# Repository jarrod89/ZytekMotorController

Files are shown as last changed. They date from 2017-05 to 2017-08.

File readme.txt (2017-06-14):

Motor control replacement board for Zytek 55KW motor.
Thanks go to James Hamond for his help in development.

Software is a modified version of Texas Instruments "Motorware" which is released under the BSD licence.

Hardware design is original work and is released under the BSD licence:

Copyright 2017 Jarrod Tuma

Redistribution and use in source and binary forms, with or without modification, are permitted provided that the following conditions are met:

1. Redistributions of source code must retain the above copyright notice, this list of conditions and the following disclaimer.

2. Redistributions in binary form must reproduce the above copyright notice, this list of conditions and the following disclaimer in the documentation and/or other materials provided with the distribution.

THIS SOFTWARE IS PROVIDED BY THE COPYRIGHT HOLDERS AND CONTRIBUTORS "AS IS" AND ANY EXPRESS OR IMPLIED WARRANTIES, INCLUDING, BUT NOT LIMITED TO, THE IMPLIED WARRANTIES OF MERCHANTABILITY AND FITNESS FOR A PARTICULAR PURPOSE ARE DISCLAIMED. IN NO EVENT SHALL THE COPYRIGHT HOLDER OR CONTRIBUTORS BE LIABLE FOR ANY DIRECT, INDIRECT, INCIDENTAL, SPECIAL, EXEMPLARY, OR CONSEQUENTIAL DAMAGES (INCLUDING, BUT NOT LIMITED TO, PROCUREMENT OF SUBSTITUTE GOODS OR SERVICES; LOSS OF USE, DATA, OR PROFITS; OR BUSINESS INTERRUPTION) HOWEVER CAUSED AND ON ANY THEORY OF LIABILITY, WHETHER IN CONTRACT, STRICT LIABILITY, OR TORT (INCLUDING NEGLIGENCE OR OTHERWISE) ARISING IN ANY WAY OUT OF THE USE OF THIS SOFTWARE, EVEN IF ADVISED OF THE POSSIBILITY OF SUCH DAMAGE.

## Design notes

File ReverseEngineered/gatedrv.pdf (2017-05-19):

High Side Feedback 1 2 | 3 4 | *

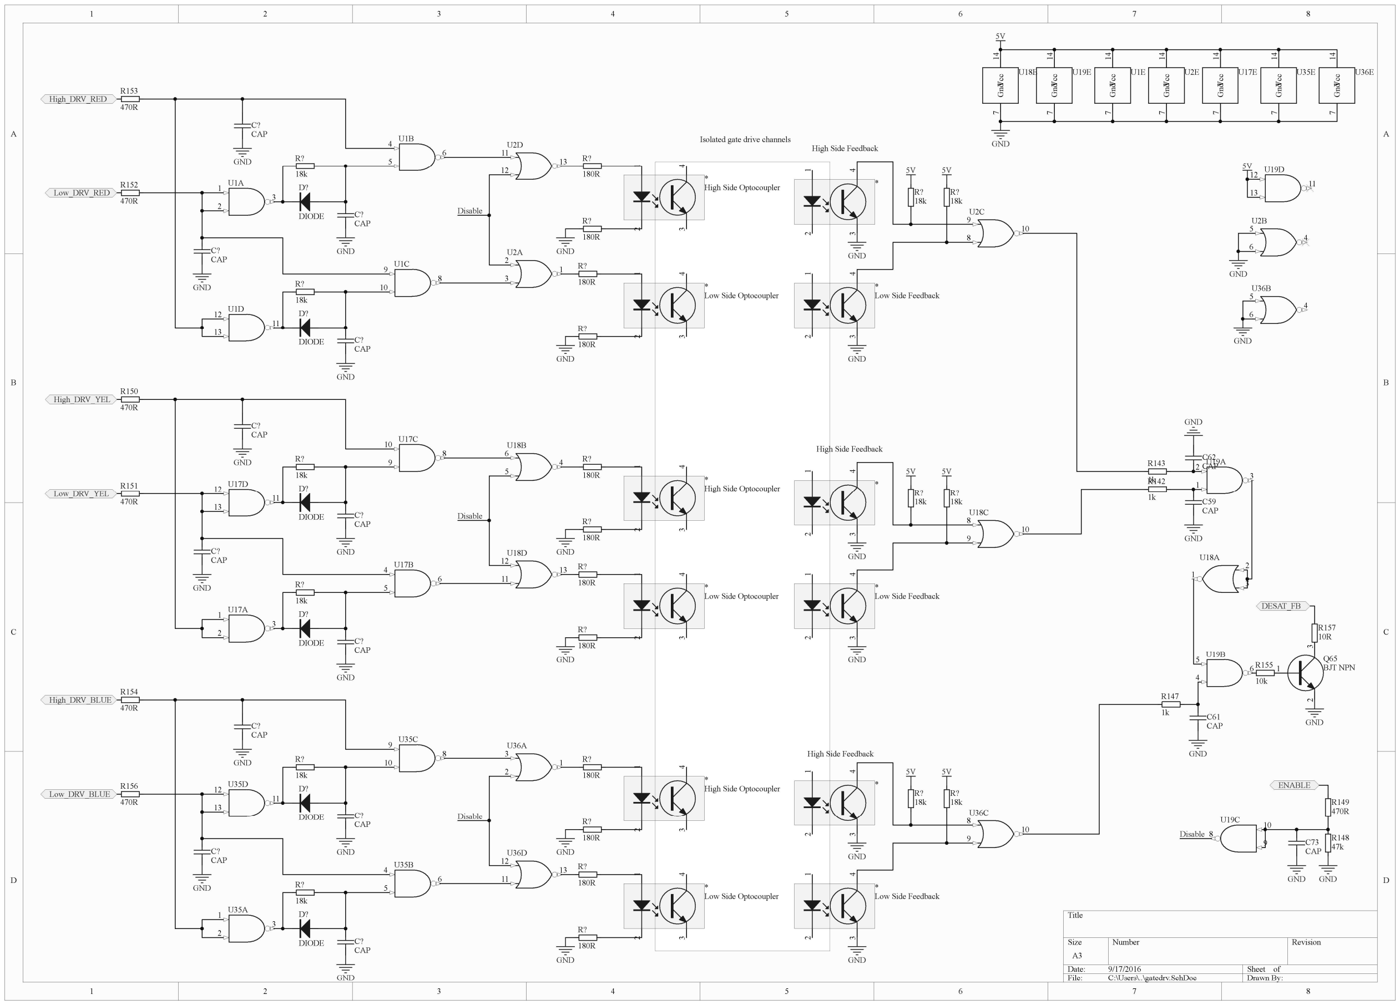
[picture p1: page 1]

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
Title
Size | Number | Revision
A3
Date: | 9/17/2016 | Sheet of
File: | C:\Users\..\gatedrv.SchDoc | Drawn By:

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
U1D | Gnd

### 7 Vcc 14

U1E

D?
DIODE

D?
DIODE

R?
18k

R153
470R

R?
18k

R152
470R

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
U2D | Gnd

### 7 Vcc 14

U2E
High_DRV_RED

Low_DRV_RED

R?
180R

R?
180R
R?
180R

R?
180R

1 23 4 *
High Side Optocoupler 1 2 | 3 4 | *

Low Side Optocoupler

GND

GND

GND ¹ ² | 3 4 | *

Low Side Feedback

R?
18k

R?
18k

5V 5V

GND

GND

R143
1k

C62
CAP
1

2
3

U19A

4

5
6

U19B

8
9

### 10 U19C

11

12
13

U19D Gnd

### 7 Vcc 14

U19E

GND

2
3

1

U18A

5

6
4

U18B

10

8
9

U18C

13
11

12

U18D | Gnd

### 7 Vcc 14

U18E

R147
1k C61 CAP

GND

R142
1k C59 CAP

GND

R155
10k

1 3 2
Q65
BJT NPN

GND

R157
10R

DESAT_FB

R148
47k C73
CAP
GND

R149
470R

GND

ENABLE

1
2

3

U17A

4
5

6

U17B

8
9

### 10 U17C

11

12
13
U17D | Gnd

### 7 Vcc 14

U17E

1
2

3

U35A

4
5

6

U35B

8

9
10

U35C

11

12
13
U35D | Gnd

### 7 Vcc 14

U35E

2

3
1

U36A

5
6

4

U36B

10

8
9

U36C

13
11

12

U36D | Gnd

### 7 Vcc 14

U36E

D?
DIODE

D?
DIODE

R?
18k

R150
470R

R?
18k

R151
470R

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
High_DRV_YEL

Low_DRV_YEL

R?
180R

R?
180R
R?
180R

R?
180R

1 23 4 *
High Side Optocoupler 1 2 | 3 4 | *

Low Side Optocoupler

GND

GND | 1 2 | 3 4 | *
High Side Feedback 1 2 | 3 4 | *

Low Side Feedback

R?
18k

R?
18k

5V 5V

GND

GND

D?
DIODE

D?
DIODE

R?
18k

R154
470R

R?
18k

R156
470R

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
High_DRV_BLUE

Low_DRV_BLUE

R?
180R

R?
180R
R?
180R

R?
180R

1 23 4 *
High Side Optocoupler 1 2 | 3 4 | *

Low Side Optocoupler

GND

GND | 1 2 | 3 4 | *
| High Side Feedback 1 2 | 3 4 | *

Low Side Feedback

R?
18k

R?
18k

5V 5V

GND

GND

5V

GND

5V

GND

Disable

Disable

Disable
Disable

Isolated gate drive channels

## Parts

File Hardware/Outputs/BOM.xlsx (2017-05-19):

Quantity | Designator | Comment | Footprint | Parameter | Manufacturer 1 | Manufacturer 2 | Manufacturer 3 | Manufacturer 4
1 | U13 | D-FLIPFLOP | SOT23-6 |  | TI SN74LVC1G175
1 | U11.2 | BTS-6143 | TO252-5-11
1 | U10 | SI88244ED-IS | SLAB-SOIC-20-WB_N |  | Silicon Labs
1 | U9 | SN74LVC1G04DBV | SOT23-5
1 | U7 | 4:1 MUX | SOIC16
2 | U5, U6 | 74AHC08 | SOIC14
4 | U4.3, U4.4, U4.5, U4.6 | OP-AMP | SOT23-5 | >1MHz, 3.3V, rail-rail. | Microchip MCP6283T | Fairchild FAN4174IS5X
6 | U3.3, U3.4, U3.5, U3.6, U8, U12 | MCP6562 | MSOP8 |  | Microchip MCP6562, Microchip MCP6562, Microchip MCP6562, Microchip MCP6562, Microchip Technology, Microchip Technology
1 | U2.2 | AP2114H-3.3TRG1DICT-ND | SOT223
1 | U1.2 | AOZ1282 | SOT23-6 | 1.2A, 4.5V-36V input, 450KHz | Alpha & Omega AOZ1282CI
1 | T1 | 2.5uH 4:11 | RM5/I
16 | R86, R87, R88, R89, R90, R91, R92, R93, R94, R96, R97, R99, R102, R103, R104, R105 | 1M | 1206 | High Voltage | Rohm Semiconductor
4 | R82, R83, R84, R85 | 130R | 0603
1 | R80 | 13.3k | 0603
2 | R79, R81 | 49.9k | 0603
1 | R78 | 100R | 0603
2 | R45.2, R47 | 47k | 0805 | <1%, Thick film, 63mW
5 | R40, R95, R98, R100, R101 | 2k | 0603 | 1%, Thick or Metal Film, 63mW, [NoValue], [NoValue], [NoValue], [NoValue]
4 | R33, R35, R37, R39 | 100k | 0603 | 1%, Thick or Metal Film, 63mW
13 | R19, R20, R21, R22, R23, R28, R29, R30, R31, R32, R34, R36, R38 | 56 | 0603 | 1%, Thick or Metal Film, 63mW, 1%, Thick or Metal Film, 63mW, 1%, Thick or Metal Film, 63mW, 1%, Thick or Metal Film, 63mW, [NoValue], 1%, Thick or Metal Film, 63mW, 1%, Thick or Metal Film, 63mW, 1%, Thick or Metal Film, 63mW, 1%, Thick or Metal Film, 63mW, 1%, Thick or Metal Film, 63mW, 1%, Thick or Metal Film, 63mW, 1%, Thick or Metal Film, 63mW, 1%, Thick or Metal Film, 63mW
4 | R11.3, R11.4, R11.5, R11.6 | 20 | 1206 | 1%, Thick or Metal Film, 63mW
5 | R10.3, R10.4, R10.5, R10.6, R49 | 100 | 0603 | 1%, Thick or Metal Film, 63mW
12 | R8.3, R8.4, R8.5, R8.6, R12.3, R12.4, R12.5, R12.6, R53.3, R53.4, R53.5, R53.6 | 3k3 | 0603 | 1%, Thick or Metal Film, 63mW
17 | R5.3, R5.4, R5.5, R5.6, R6.3, R6.4, R6.5, R6.6, R15, R16, R17, R18, R24, R25, R26, R27, R44.2 | 10k | 0603 | 1%, Thick or Metal Film, 63mW, 1%, Thick or Metal Film, 63mW, 1%, Thick or Metal Film, 63mW, 1%, Thick or Metal Film, 63mW, 1%, Thick or Metal Film, 63mW, 1%, Thick or Metal Film, 63mW, 1%, Thick or Metal Film, 63mW, 1%, Thick or Metal Film, 63mW, [NoValue], [NoValue], [NoValue], [NoValue], [NoValue], [NoValue], [NoValue], [NoValue], 1%, Thick or Metal Film, 63mW
8 | R4.3, R4.4, R4.5, R4.6, R7.3, R7.4, R7.5, R7.6 | 220R | 0603 | 1%, Thick or Metal Film, 63mW
1 | R3.2 | 68k | 0603 | <1%, Thick film, 63mW
1 | R2.2 | 13k | 0603 | <1%, Thick film, 63mW
24 | R1.2, R9.3, R9.4, R9.5, R9.6, R13.3, R13.4, R13.5, R13.6, R14, R41, R42, R43, R46, R48, R50, R51, R52, R54, R56, R106, R107, R108, R109 | 1k | 0603 | <1%, Thick film, 63mW, 1%, Thick or Metal Film, 63mW, 1%, Thick or Metal Film, 63mW, 1%, Thick or Metal Film, 63mW, 1%, Thick or Metal Film, 63mW, 1%, Thick or Metal Film, 63mW, 1%, Thick or Metal Film, 63mW, 1%, Thick or Metal Film, 63mW, 1%, Thick or Metal Film, 63mW, 1%, Thick or Metal Film, 63mW, [NoValue], [NoValue], [NoValue], [NoValue], [NoValue], [NoValue], [NoValue], [NoValue], [NoValue], [NoValue], [NoValue], [NoValue], [NoValue], [NoValue]
1 | Q1.2 | nmos | SOT23
8 | P1, P2, P3, P4, P5, P6, P7, P8 | HEADER 10 | HDR10
4 | L8, L9, L10, L11 | 1m | 0805 | Inductor, 4u7, 20%, >100mA | Taiyo Yuden LBR2012T4R7M | Abracon AIML-0805-4R7K-T | Bourns CV201210-4R7K | TDK MLZ2012N4R7L
1 | L6 | 4u7 | 0805 | Inductor, 4u7, 20%, >100mA | Taiyo Yuden LBR2012T4R7M | Abracon AIML-0805-4R7K-T | Bourns CV201210-4R7K | TDK MLZ2012N4R7L
2 | L1.2, L2.2 | 22u, 1A | 2220 | INDUCTOR 22uH >1A 1210
1 | J13 | HEADER 5 | HDR5-5mm
1 | J6 | Header 17X2 | HDR2X17_2mm
1 | J5 | Header 16 | HDR1X16
1 | J1 | Header 25X2 | HDR2X20_2mm
1 | F1.2 | ?A | 1206
3 | D13, D14, D15 | LED | 0603_LED
9 | D5, D6, D7, D8, D9, D10, D11, D12, D16 | DIODE | D-0603
1 | D4 | DIODE SCHOTTKY | SOD323-AK
2 | D3, D17 |  | SOD323-AK | Signal, >=200mA, SOD323, Vr>=75V
1 | D2.2 | Schottky | DO214AC | DIODE SHOTTKY >30V >0.2A | Micro Commercial Co SD103AWS-TP
1 | D1.2 | ZENER | DO214AC
4 | C74, C75, C76, C77 | 220n | 0603
1 | C72 | 1n5 | 0603 | 10n, 0603, 50V, <20%, X7R Ceramic | Murata GRM188R71H103KA01D | AVX 06035C103KAT2A | TDK C1608X7R1H103J
1 | C69 | 100p | 0603 | 10n, 0603, 50V, <20%, X7R Ceramic | Murata GRM188R71H103KA01D | AVX 06035C103KAT2A | TDK C1608X7R1H103J
4 | C22.3, C22.4, C22.5, C22.6 | 3n3 | 0603
12 | C21.3, C21.4, C21.5, C21.6, C73, C78, C79, C80, C81, C82, C83, C84 | 470p | 0603
12 | C9.2, C16.2, C26, C27, C28, C29, C30, C31, C32, C33, C68, C71 | 10n | 0603 | 100n, 0603, 50V, <20%, X7R Ceramic, 10n, 0603, 50V, <20%, X7R Ceramic, [NoValue], [NoValue], [NoValue], [NoValue], [NoValue], [NoValue], [NoValue], [NoValue], [NoValue], [NoValue] | Murata GRM188R71H104KA93D, Murata GRM188R71H103KA01D, [NoValue], [NoValue], [NoValue], [NoValue], [NoValue], [NoValue], [NoValue], [NoValue], [NoValue], [NoValue] | TDK C1608X7R1H104K, AVX 06035C103KAT2A, [NoValue], [NoValue], [NoValue], [NoValue], [NoValue], [NoValue], [NoValue], [NoValue], [NoValue], [NoValue] | AVX 06035C104KAT2A, TDK C1608X7R1H103J, [NoValue], [NoValue], [NoValue], [NoValue], [NoValue], [NoValue], [NoValue], [NoValue], [NoValue], [NoValue] | Kemet C0603C104J5RACTU-ND
44 | C4.2, C5.2, C8.2, C12.2, C14.2, C17.3, C17.4, C17.5, C17.6, C18.3, C18.4, C18.5, C18.6, C19.3, C19.4, C19.5, C19.6, C20.3, C20.4, C20.5, C20.6, C23.3, C23.4, C23.5, C23.6, C24.3, C24.4, C24.5, C24.6, C34, C35, C36, C37, C38, C39, C40, C41, C42, C43, C66, C67, C70, C85, C86 | 100n | 0603 | 100n, 0603, 50V, <20%, X7R Ceramic, 100n, 0603, 50V, <20%, X7R Ceramic, 100n, 0603, 50V, <20%, X7R Ceramic, [NoValue], 470n, 0603, >=16V, <20%, X7R Ceramic, [NoValue], [NoValue], [NoValue], [NoValue], [NoValue], [NoValue], [NoValue], [NoValue], [NoValue], [NoValue], [NoValue], [NoValue], [NoValue], [NoValue], [NoValue], [NoValue], [NoValue], [NoValue], [NoValue], [NoValue], [NoValue], [NoValue], [NoValue], [NoValue], [NoValue], [NoValue], [NoValue], [NoValue], [NoValue], [NoValue], [NoValue], [NoValue], [NoValue], [NoValue], [NoValue], [NoValue], [NoValue], [NoValue], [NoValue] | Murata GRM188R71H104KA93D, Murata GRM188R71H104KA93D, Murata GRM188R71H104KA93D, [NoValue], Murata GCM188R71C474KA55D, [NoValue], [NoValue], [NoValue], [NoValue], [NoValue], [NoValue], [NoValue], [NoValue], [NoValue], [NoValue], [NoValue], [NoValue], [NoValue], [NoValue], [NoValue], [NoValue], [NoValue], [NoValue], [NoValue], [NoValue], [NoValue], [NoValue], [NoValue], [NoValue], [NoValue], [NoValue], [NoValue], [NoValue], [NoValue], [NoValue], [NoValue], [NoValue], [NoValue], [NoValue], [NoValue], [NoValue], [NoValue], [NoParam], [NoParam] | TDK C1608X7R1H104K, TDK C1608X7R1H104K, TDK C1608X7R1H104K, [NoValue], Taiyo EMK107B7474KA-T, [NoValue], [NoValue], [NoValue], [NoValue], [NoValue], [NoValue], [NoValue], [NoValue], [NoValue], [NoValue], [NoValue], [NoValue], [NoValue], [NoValue], [NoValue], [NoValue], [NoValue], [NoValue], [NoValue], [NoValue], [NoValue], [NoValue], [NoValue], [NoValue], [NoValue], [NoValue], [NoValue], [NoValue], [NoValue], [NoValue], [NoValue], [NoValue], [NoValue], [NoValue], [NoValue], [NoValue], [NoValue], [NoParam], [NoParam] | AVX 06035C104KAT2A, AVX 06035C104KAT2A, AVX 06035C104KAT2A, [NoValue], Kemet C0603C474K4RACTU, C0603C474K4RAC, [NoValue], [NoValue], [NoValue], [NoValue], [NoValue], [NoValue], [NoValue], [NoValue], [NoValue], [NoValue], [NoValue], [NoValue], [NoValue], [NoValue], [NoValue], [NoValue], [NoValue], [NoValue], [NoValue], [NoValue], [NoValue], [NoValue], [NoValue], [NoValue], [NoValue], [NoValue], [NoValue], [NoValue], [NoValue], [NoValue], [NoValue], [NoValue], [NoValue], [NoValue], [NoValue], [NoValue], [NoValue], [NoParam], [NoParam] | Kemet C0603C104J5RACTU-ND, Kemet C0603C104J5RACTU-ND, Kemet C0603C104J5RACTU-ND, [NoParam], TDK C1608X7R1C474M, [NoParam], [NoParam], [NoParam], [NoParam], [NoParam], [NoParam], [NoParam], [NoParam], [NoParam], [NoParam], [NoParam], [NoParam], [NoParam], [NoParam], [NoParam], [NoParam], [NoParam], [NoParam], [NoParam], [NoParam], [NoParam], [NoParam], [NoParam], [NoParam], [NoParam], [NoParam], [NoParam], [NoParam], [NoParam], [NoParam], [NoParam], [NoParam], [NoParam], [NoParam], [NoParam], [NoParam], [NoParam], [NoParam], [NoParam]
13 | C1.2, C2.2, C3.2, C6.2, C7.2, C10.2, C11.2, C13.2, C15.2, C25, C63, C64, C65 | 10u | 0805 | [NoValue], [NoValue], [NoValue], 10uF, 0805, =>6.3V, <=10%, X5R Ceramic, 10uF, 0805, =>6.3V, <=10%, X5R Ceramic, 10uF, 0805, =>6.3V, <=10%, X5R Ceramic, 10uF, 0805, =>6.3V, <=10%, X5R Ceramic, 10uF, 0805, =>6.3V, <=10%, X5R Ceramic, [NoValue], [NoValue], [NoValue], [NoValue], [NoValue]

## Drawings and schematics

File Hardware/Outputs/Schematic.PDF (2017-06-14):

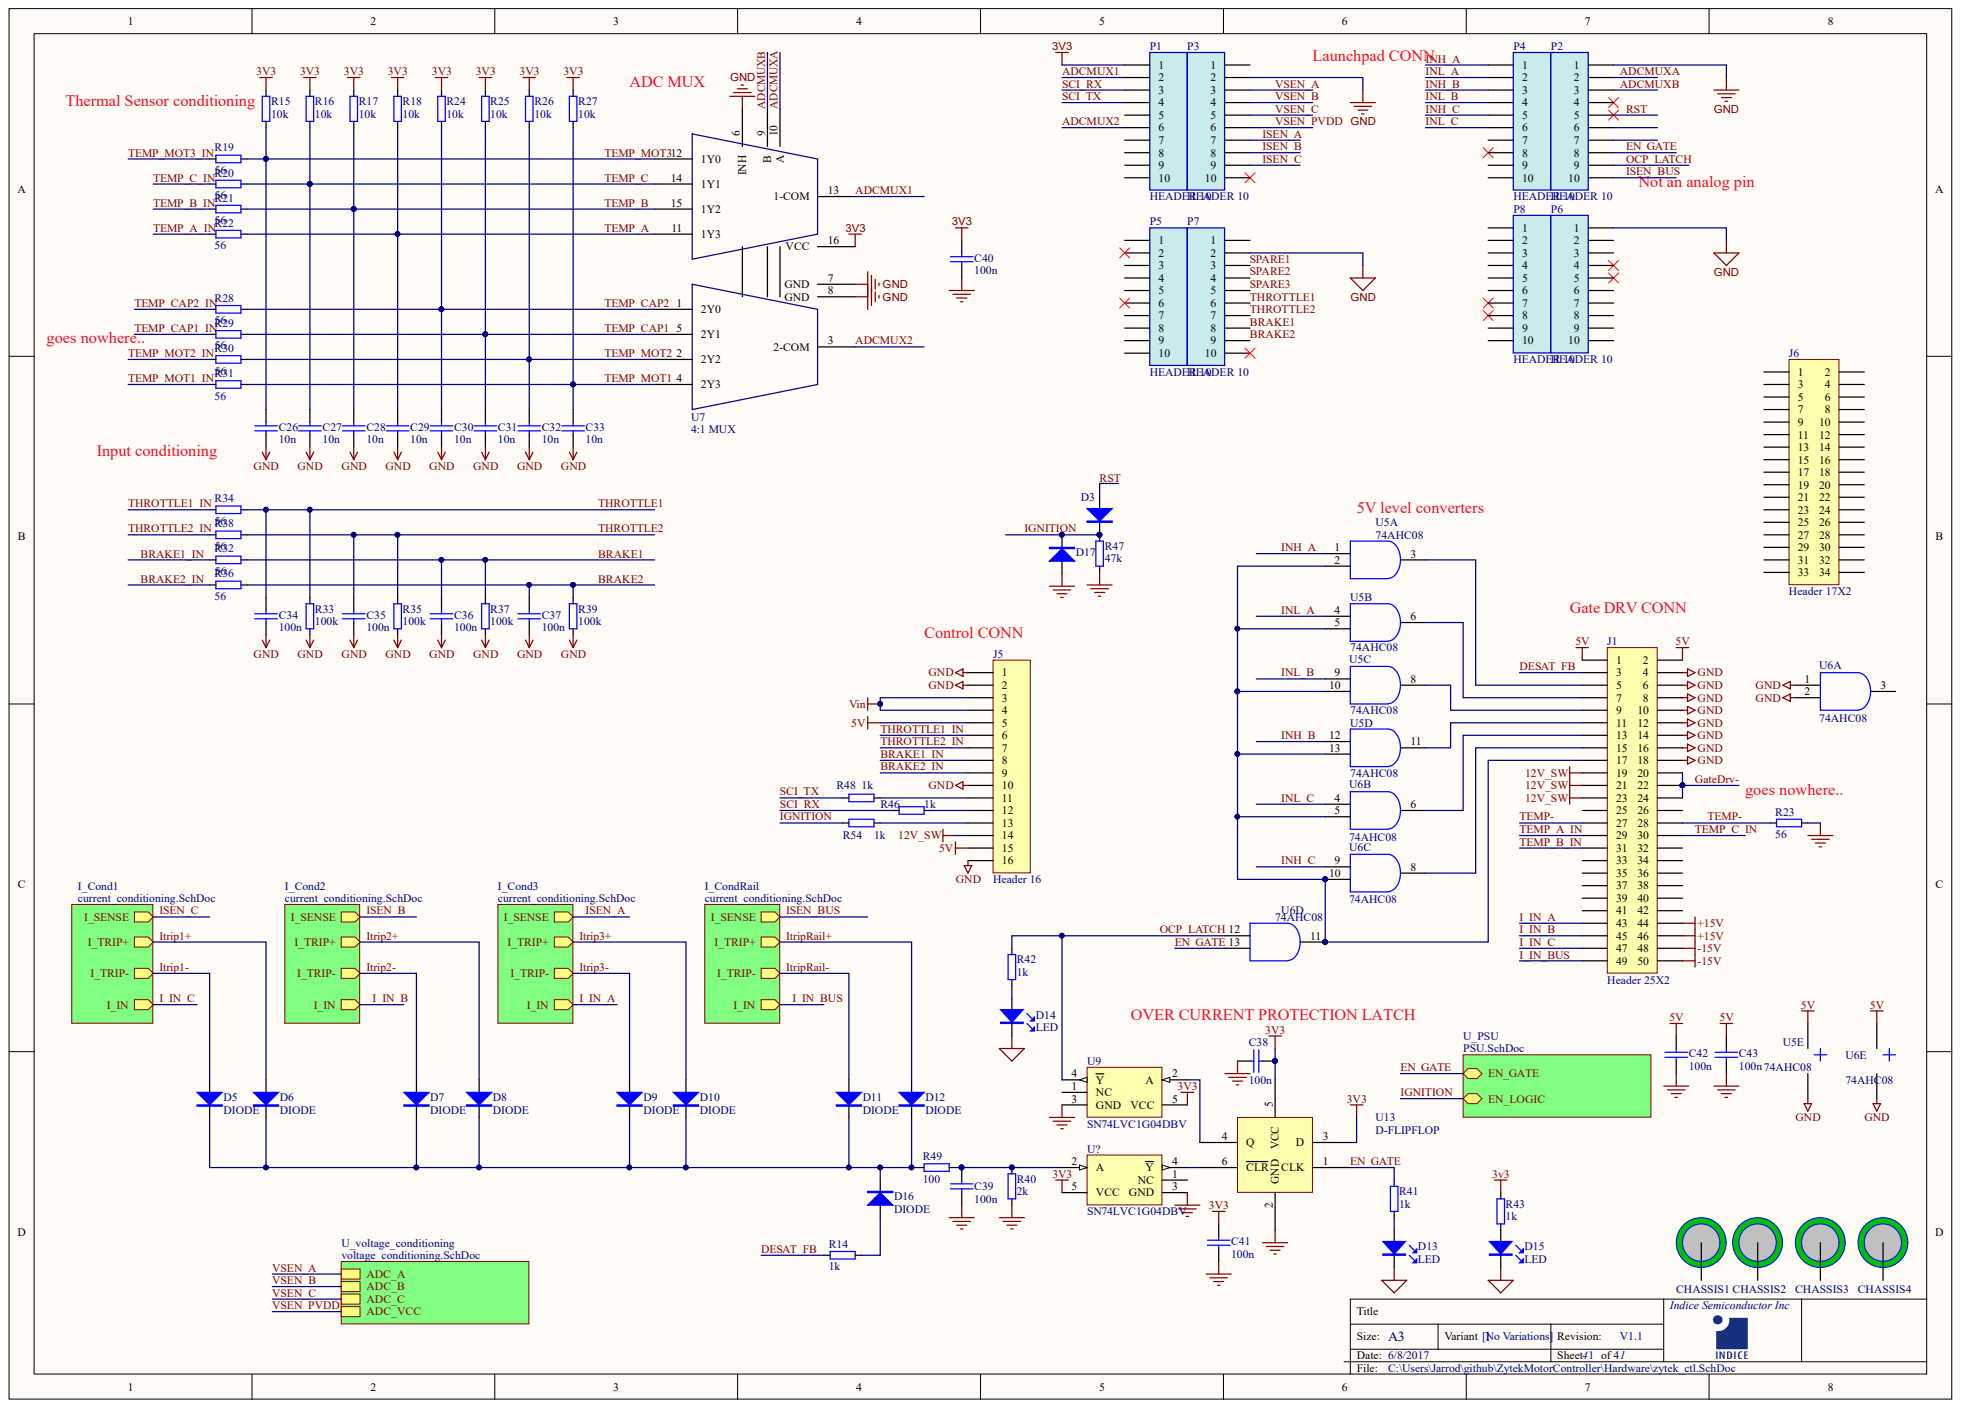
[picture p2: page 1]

OVER CURRENT PROTECTION LATCH

Title | Indice Semiconductor Inc

Size: A3 | Variant [No Variations] | Revision: V1.1
Date: 6/8/2017 | | Sheet 41 of 41

C:\Users\Jarrod\github\ZytekMotorController\Hardware\zytek_ctl.SchDoc

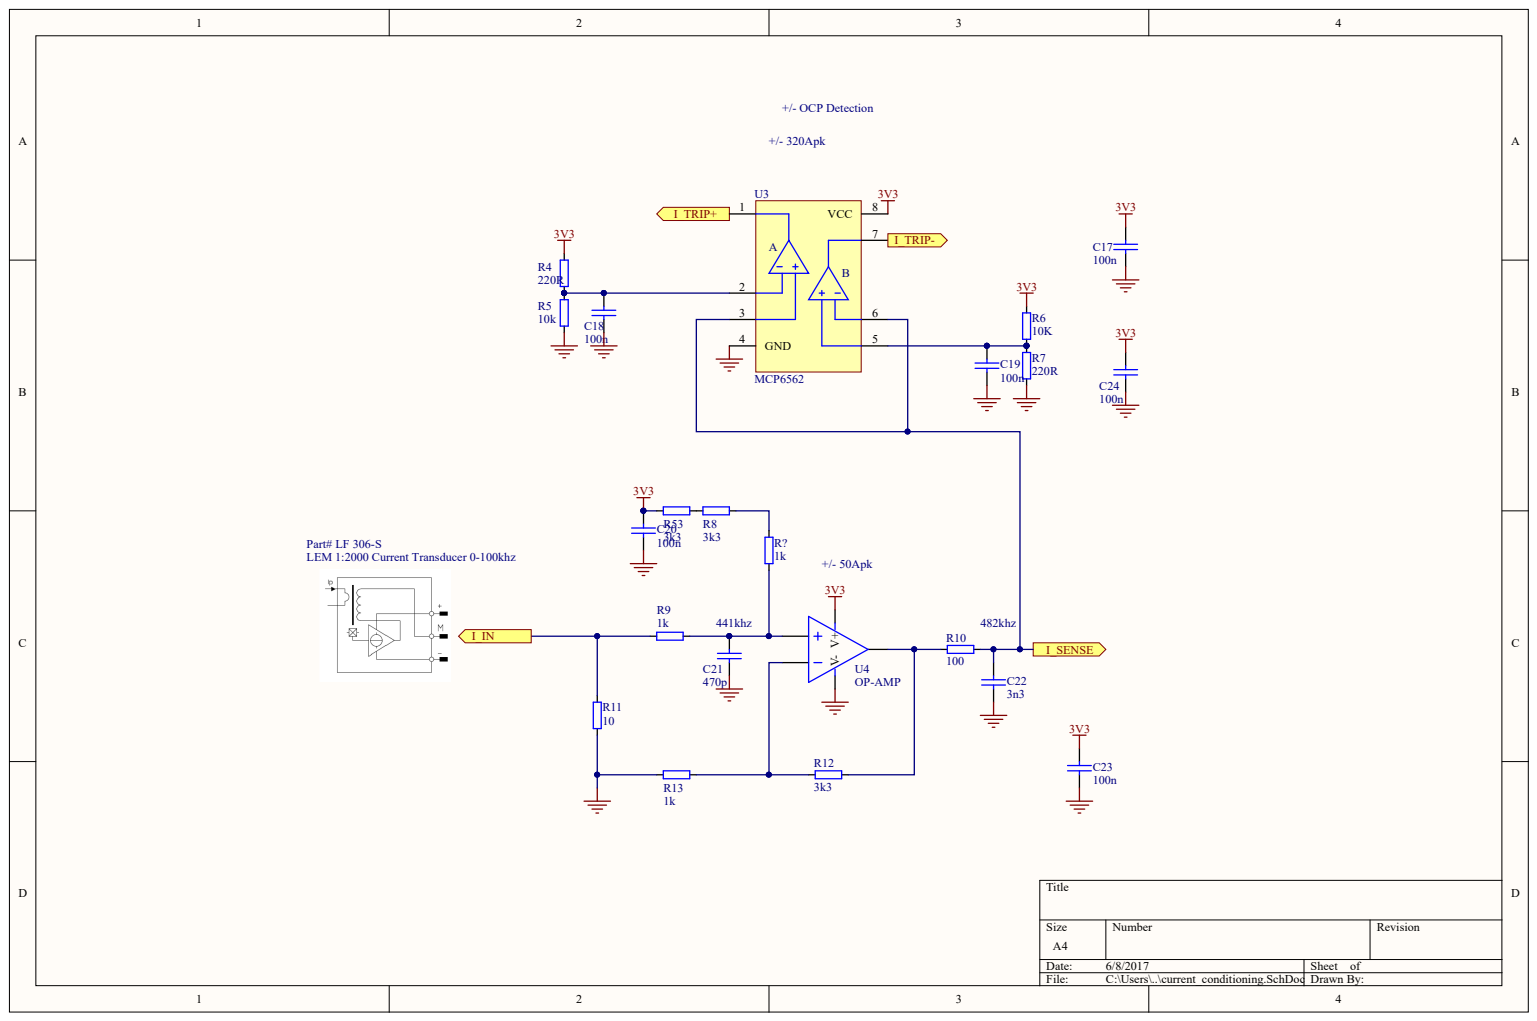
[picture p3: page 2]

U4 OP-AMP

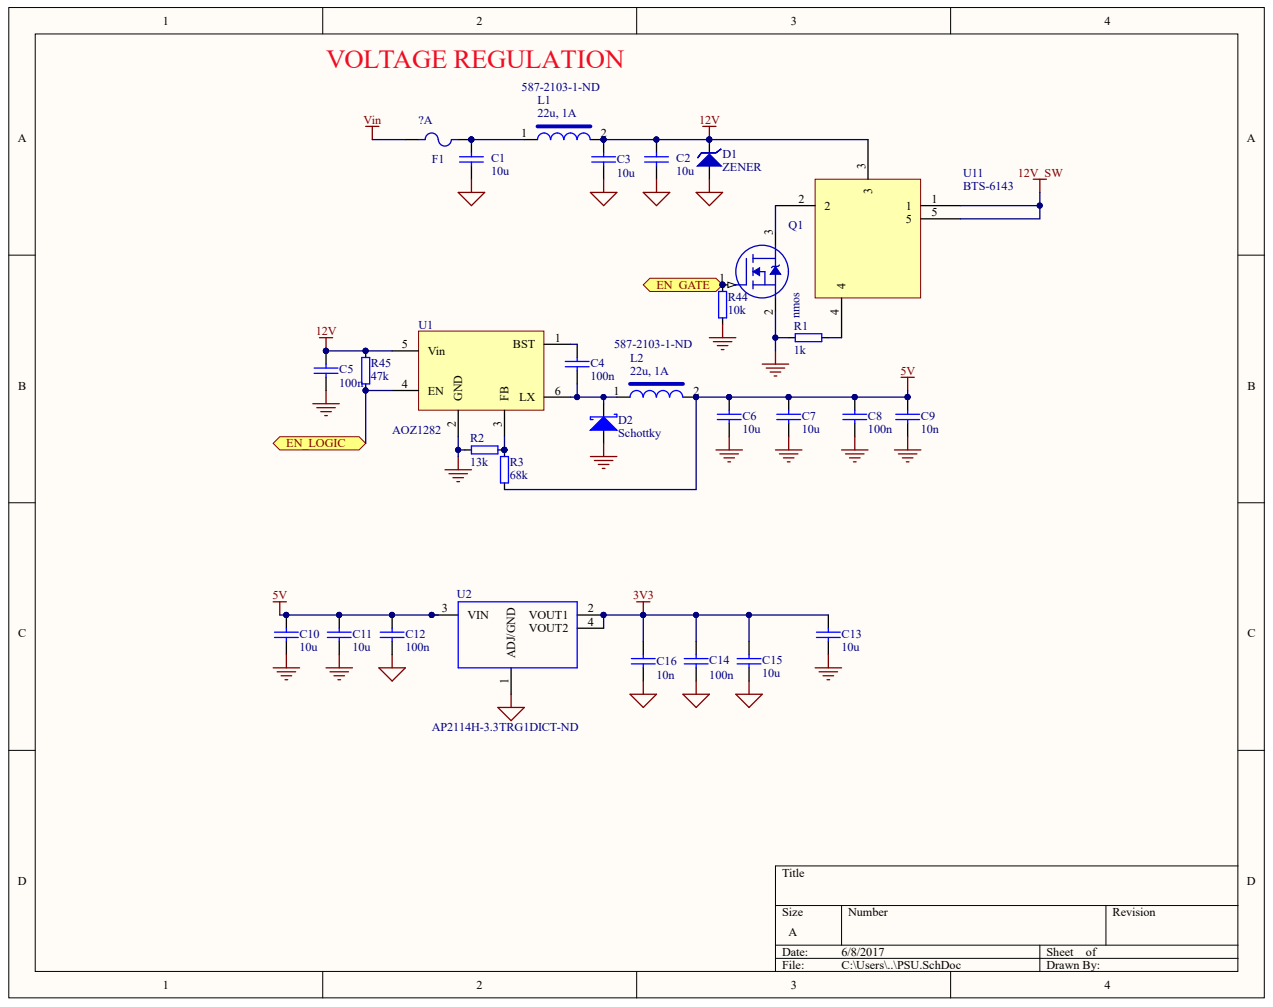
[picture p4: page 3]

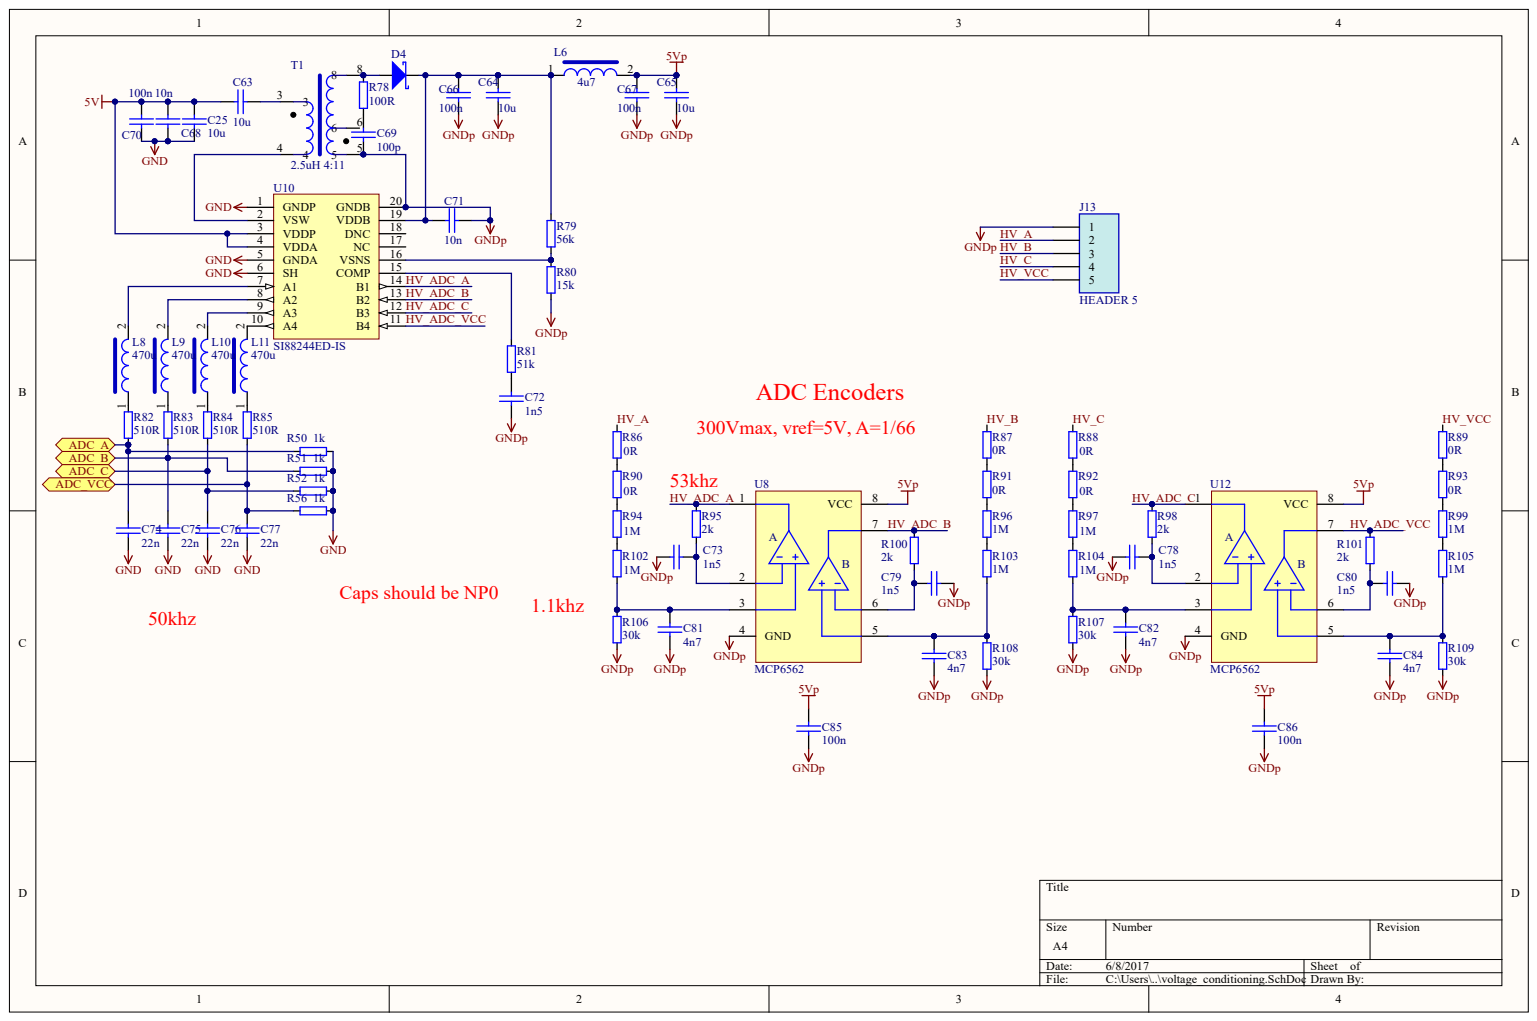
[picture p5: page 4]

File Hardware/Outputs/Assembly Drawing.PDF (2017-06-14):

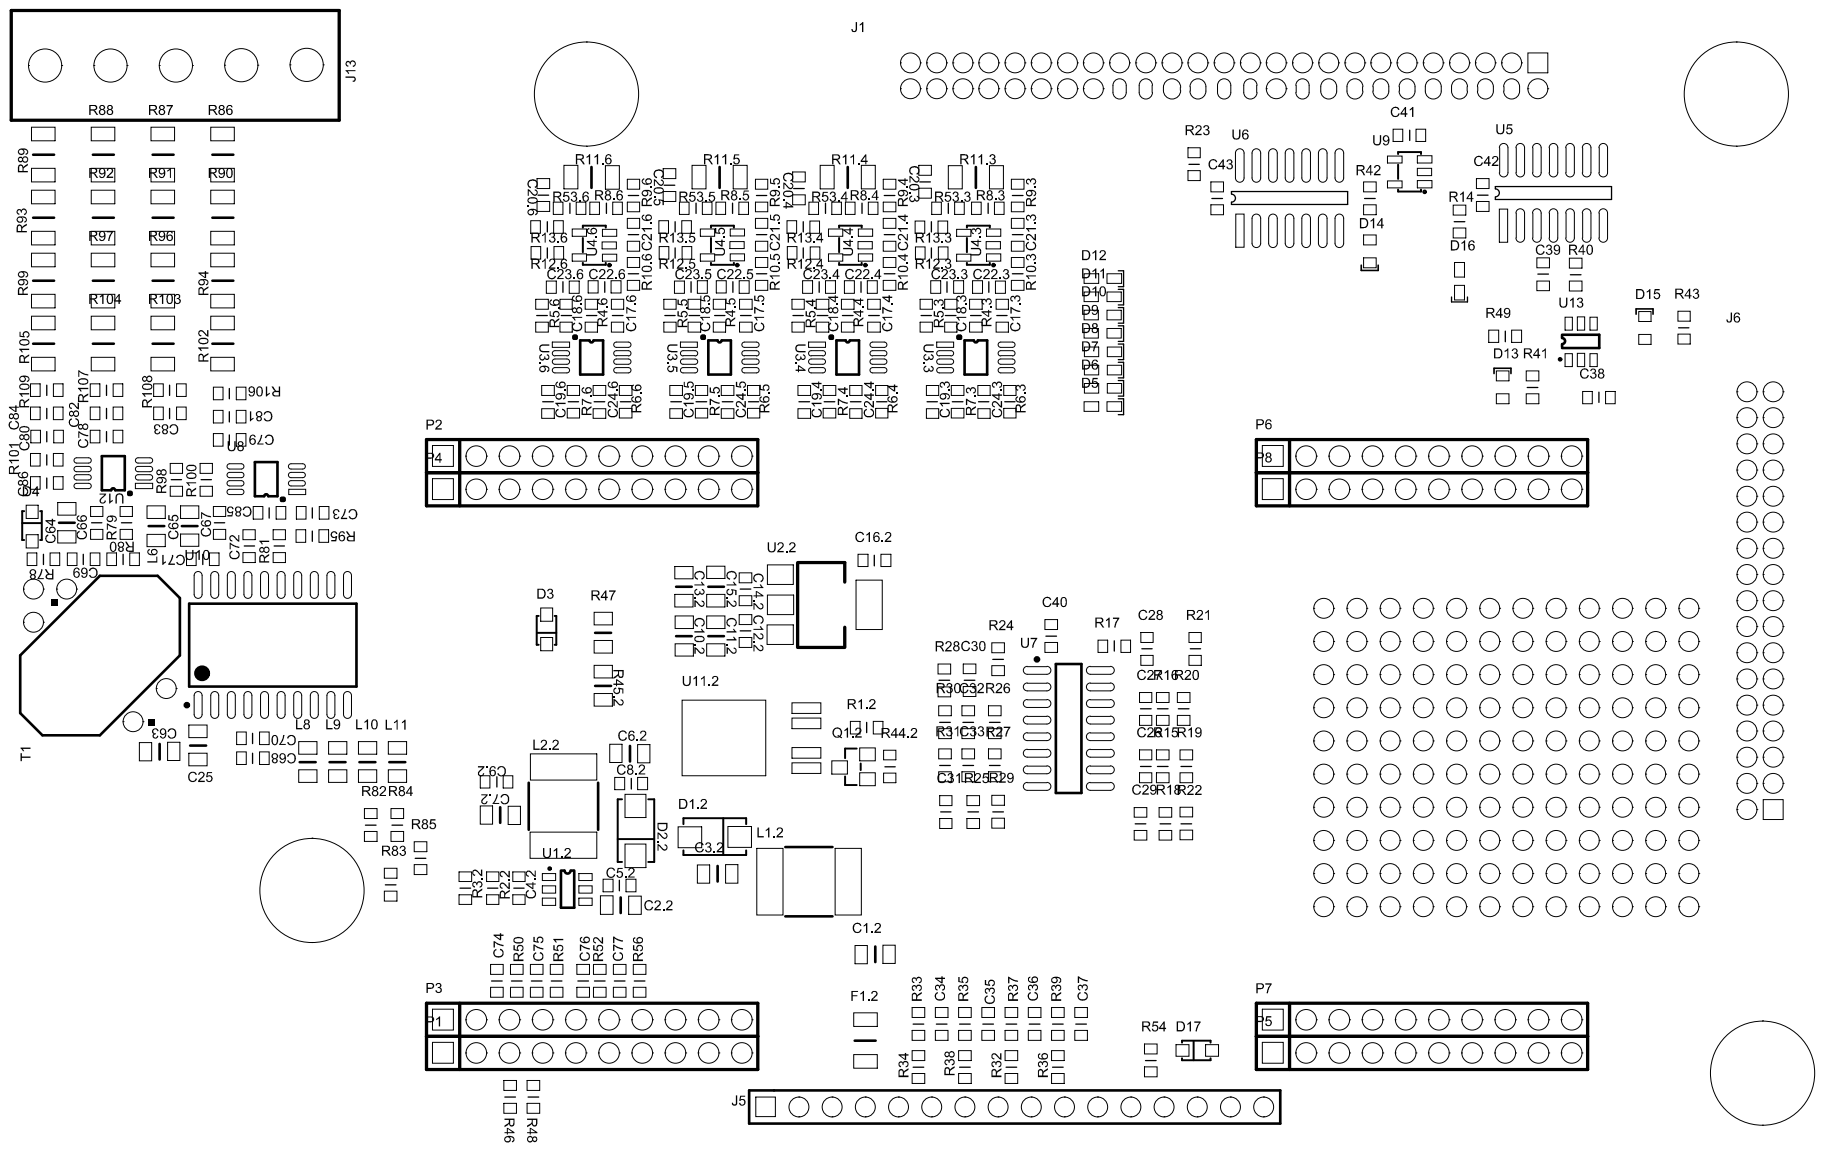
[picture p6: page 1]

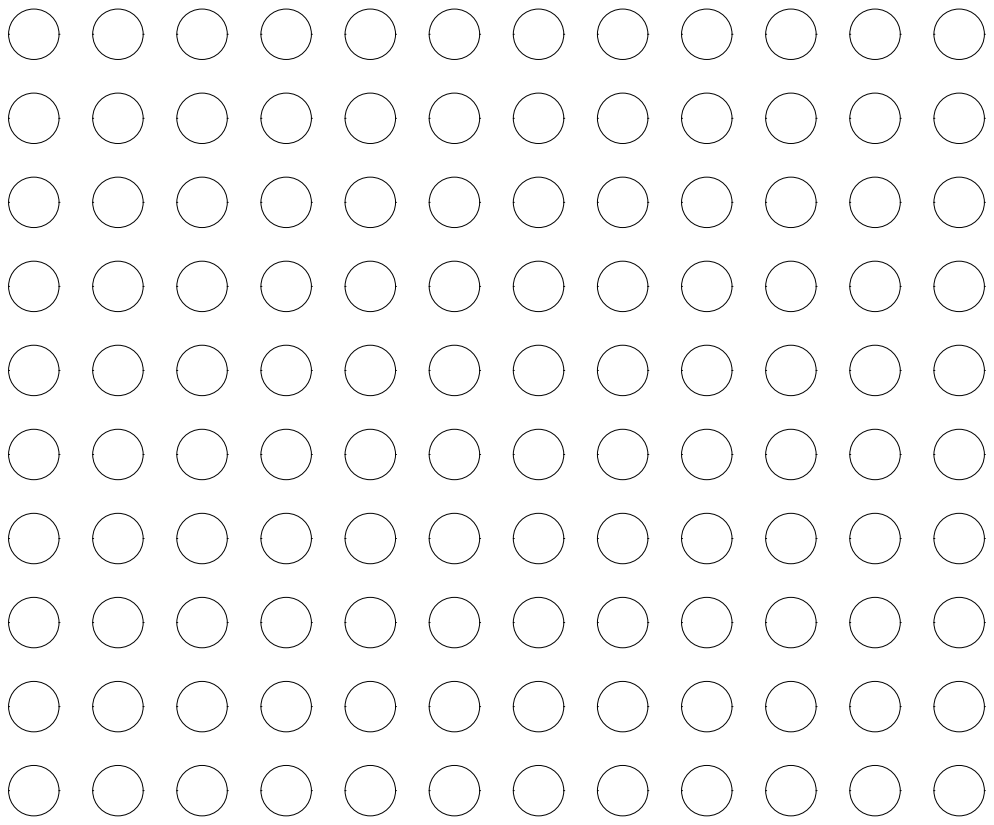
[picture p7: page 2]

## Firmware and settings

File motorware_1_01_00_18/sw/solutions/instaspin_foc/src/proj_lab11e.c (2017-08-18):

/* --COPYRIGHT--,BSD
 * Copyright (c) 2015, Texas Instruments Incorporated
 * All rights reserved.
 *
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
 * *  Redistributions of source code must retain the above copyright
 *    notice, this list of conditions and the following disclaimer.
 *
 * *  Redistributions in binary form must reproduce the above copyright
 *    notice, this list of conditions and the following disclaimer in the
 *    documentation and/or other materials provided with the distribution.
 *
 * *  Neither the name of Texas Instruments Incorporated nor the names of
 *    its contributors may be used to endorse or promote products derived
 *    from this software without specific prior written permission.
 *
 * THIS SOFTWARE IS PROVIDED BY THE COPYRIGHT HOLDERS AND CONTRIBUTORS "AS IS"
 * AND ANY EXPRESS OR IMPLIED WARRANTIES, INCLUDING, BUT NOT LIMITED TO,
 * THE IMPLIED WARRANTIES OF MERCHANTABILITY AND FITNESS FOR A PARTICULAR
 * PURPOSE ARE DISCLAIMED. IN NO EVENT SHALL THE COPYRIGHT OWNER OR
 * CONTRIBUTORS BE LIABLE FOR ANY DIRECT, INDIRECT, INCIDENTAL, SPECIAL,
 * EXEMPLARY, OR CONSEQUENTIAL DAMAGES (INCLUDING, BUT NOT LIMITED TO,
 * PROCUREMENT OF SUBSTITUTE GOODS OR SERVICES; LOSS OF USE, DATA, OR PROFITS;
 * OR BUSINESS INTERRUPTION) HOWEVER CAUSED AND ON ANY THEORY OF LIABILITY,
 * WHETHER IN CONTRACT, STRICT LIABILITY, OR TORT (INCLUDING NEGLIGENCE OR
 * OTHERWISE) ARISING IN ANY WAY OUT OF THE USE OF THIS SOFTWARE,
 * EVEN IF ADVISED OF THE POSSIBILITY OF SUCH DAMAGE.
 * --/COPYRIGHT--*/
//! \file   solutions/instaspin_foc/src/proj_lab011e.c
//! \brief Hall sensor start-up with transition to FAST for InstaSPIN-FOC
//!
//! (C) Copyright 2015, Texas Instruments, Inc.

//! \defgroup PROJ_LAB11e PROJ_LAB11e
//@{

//! \defgroup PROJ_LAB11e_OVERVIEW Project Overview
//!
//! Hall sensor start-up with transition to FAST for InstaSPIN-FOC
//! 
//!

// **************************************************************************
// the includes

// system includes
#include <math.h>
#include "main.h"


#ifdef FLASH
#pragma CODE_SECTION(mainISR,"ramfuncs");
#pragma CODE_SECTION(runSetTrigger,"ramfuncs");
#pragma CODE_SECTION(runFieldWeakening,"ramfuncs");
#pragma CODE_SECTION(runCurrentReconstruction,"ramfuncs");
#pragma CODE_SECTION(angleDelayComp,"ramfuncs");
#pragma CODE_SECTION(HALLBLDC_State_Check,"ramfuncs");
#pragma CODE_SECTION(HALLBLDC_Ctrl_PwmSet,"ramfuncs");
#pragma CODE_SECTION(HALLBLDC_Ctrl_Run,"ramfuncs");
#endif

// Include header files used in the main function

// **************************************************************************
// the defines

// **************************************************************************
// the globals

CLARKE_Handle   clarkeHandle_I;               //!< the handle for the current Clarke transform
CLARKE_Obj      clarke_I;                     //!< the current Clarke transform object

CLARKE_Handle   clarkeHandle_V;               //!< the handle for the voltage Clarke transform
CLARKE_Obj      clarke_V;                     //!< the voltage Clarke transform object

EST_Handle      estHandle;                    //!< the handle for the estimator

FW_Handle       fwHandle;
FW_Obj          fw;

PID_Obj         pid[4];                       //!< three handles for PID controllers 0 - Speed, 1 - Id, 2 - Iq
PID_Handle      pidHandle[4];                 //!< three objects for PID controllers 0 - Speed, 1 - Id, 2 - Iq
uint16_t        pidCntSpeed;                  //!< count variable to decimate the execution of the speed PID controller

IPARK_Handle    iparkHandle;                  //!< the handle for the inverse Park transform
IPARK_Obj       ipark;                        //!< the inverse Park transform object

FILTER_FO_Handle  filterHandle[6];            //!< the handles for the 3-current and 3-voltage filters for offset calculation
FILTER_FO_Obj     filter[6];                  //!< the 3-current and 3-voltage filters for offset calculation

SVGENCURRENT_Obj     svgencurrent;
SVGENCURRENT_Handle  svgencurrentHandle;

SVGEN_Handle    svgenHandle;                  //!< the handle for the space vector generator
SVGEN_Obj       svgen;                        //!< the space vector generator object

TRAJ_Handle     trajHandle_Id;                //!< the handle for the id reference trajectory
TRAJ_Obj        traj_Id;                      //!< the id reference trajectory object

TRAJ_Handle     trajHandle_spd;               //!< the handle for the speed reference trajectory
TRAJ_Obj        traj_spd;                     //!< the speed reference trajectory object

#ifdef CSM_ENABLE
#pragma DATA_SECTION(halHandle,"rom_accessed_data");
#endif

HAL_Handle      halHandle;                    //!< the handle for the hardware abstraction layer (HAL)

HAL_PwmData_t   gPwmData = {_IQ(0.0), _IQ(0.0), _IQ(0.0)};       //!< contains the three pwm values -1.0 - 0%, 1.0 - 100%

HAL_AdcData_t   gAdcData;                     //!< contains three current values, three voltage values and one DC buss value

MATH_vec3       gOffsets_I_pu = {_IQ(0.0), _IQ(0.0), _IQ(0.0)};  //!< contains the offsets for the current feedback

MATH_vec3       gOffsets_V_pu = {_IQ(0.0), _IQ(0.0), _IQ(0.0)};  //!< contains the offsets for the voltage feedback

MATH_vec2       gIdq_ref_pu = {_IQ(0.0), _IQ(0.0)};              //!< contains the Id and Iq references

MATH_vec2       gVdq_out_pu = {_IQ(0.0), _IQ(0.0)};              //!< contains the output Vd and Vq from the current controllers

MATH_vec2       gIdq_pu = {_IQ(0.0), _IQ(0.0)};                  //!< contains the Id and Iq measured values

#ifdef CSM_ENABLE
#pragma DATA_SECTION(gUserParams,"rom_accessed_data");
#endif

USER_Params     gUserParams;

volatile MOTOR_Vars_t gMotorVars = MOTOR_Vars_INIT;   //!< the global motor variables that are defined in main.h and used for display in the debugger's watch window

#ifdef FLASH
// Used for running BackGround in flash, and ISR in RAM
extern uint16_t *RamfuncsLoadStart, *RamfuncsLoadEnd, *RamfuncsRunStart;

#ifdef CSM_ENABLE
extern uint16_t *econst_start, *econst_end, *econst_ram_load;
extern uint16_t *switch_start, *switch_end, *switch_ram_load;
#endif
#endif


MATH_vec3 gIavg = {_IQ(0.0), _IQ(0.0), _IQ(0.0)};
uint16_t gIavg_shift = 1;
MATH_vec3 gPwmData_prev = {_IQ(0.0), _IQ(0.0), _IQ(0.0)};

#ifdef DRV8301_SPI
// Watch window interface to the 8301 SPI
DRV_SPI_8301_Vars_t gDrvSpi8301Vars;
#endif

#ifdef DRV8305_SPI
// Watch window interface to the 8305 SPI
DRV_SPI_8305_Vars_t gDrvSpi8305Vars;
#endif

// define CPU time
CPU_TIME_Obj     cpu_time;
CPU_TIME_Handle  cpu_timeHandle;

HAL_DacData_t gDacData;

_iq gFlux_pu_to_Wb_sf;

_iq gFlux_pu_to_VpHz_sf;

_iq gTorque_Ls_Id_Iq_pu_to_Nm_sf;

_iq gTorque_Flux_Iq_pu_to_Nm_sf;

_iq gSpeed_krpm_to_pu_sf = _IQ((float_t)USER_MOTOR_NUM_POLE_PAIRS * 1000.0 / (USER_IQ_FULL_SCALE_FREQ_Hz * 60.0));

_iq gSpeed_hz_to_krpm_sf = _IQ(60.0 / (float_t)USER_MOTOR_NUM_POLE_PAIRS / 1000.0);

_iq gIs_Max_squared_pu = _IQ((USER_MOTOR_MAX_CURRENT * USER_MOTOR_MAX_CURRENT) / (USER_IQ_FULL_SCALE_CURRENT_A * USER_IQ_FULL_SCALE_CURRENT_A));

uint32_t gOffsetCalcCount = 0;

uint16_t gTrjCnt = 0;

volatile bool gFlag_enableRsOnLine = false;

volatile bool gFlag_updateRs = false;

volatile _iq gRsOnLineFreq_Hz = _IQ(0.2);

volatile _iq gRsOnLineId_mag_A = _IQ(0.5);

volatile _iq gRsOnLinePole_Hz = _IQ(0.2);

//variable
_iq speed_pid_out = _IQ(0.0);
_iq angle_est_pu = _IQ(0.0);
_iq speed_est_pu = _IQ(0.0);
_iq angle_pu = _IQ(0.0);
_iq speed_pu = _IQ(0.0);

//BLDC current loop
_iq gHall_BLDC_Is_fdb_pu = _IQ(0.0);
_iq gHall_BLDC_Is_ref_pu = _IQ(0.0);
_iq gHall_PwmDuty = _IQ(0.0);

// Coefficient for pid regulator switch from Hall to Fast
_iq gHall2Fast_Spd_Coef = _IQ(1.0);
_iq gHall2Fast_Iq_coef = _IQ(0.50);
_iq gHall2Fast_Ui_coef = _IQ(0.50);

// Coefficient for pid regulator switch from Fast to Hall
_iq gFast2Hall_Spd_coef = _IQ(1.0);
_iq gFast2Hall_Iq_coef = _IQ(0.0);
_iq gFast2Hall_Ui_coef = _IQ(2.0);

// BLDC speed
_iq gHall_speed_fdb_pu = _IQ(0.0);
_iq gHall_speed_FastToBldc_low_pu  = _IQ(0.400*USER_MOTOR_NUM_POLE_PAIRS*1000.0/(USER_IQ_FULL_SCALE_FREQ_Hz * 60.0));		// 400rpm
_iq gHall_speed_BldcToFast_high_pu = _IQ(0.750*USER_MOTOR_NUM_POLE_PAIRS*1000.0/(USER_IQ_FULL_SCALE_FREQ_Hz * 60.0));		// 750rpm

uint16_t gHall_PwmState = 0;

uint16_t gHall_GpioData = 0;
int16_t gHall_State = 0;
int16_t gHall_PrevState = 0;
int16_t gHall_LastState = 0;
int16_t gHall_State_delta = 0;

uint16_t gHall_dir = 0;
uint16_t gHall_dir_prev = 0;
uint16_t gHall_dir_change = 0;

uint16_t gHall_BLDC_Flag_Is_fdb = 0;
uint16_t gHall_PwmIndex[8] = {4, 1, 5, 6, 3, 2, 4, 1};

bool gHall_Flag_EnableBldc = true;
bool gHall_Flag_EnableStartup = true;		// true->enable hall startup
//bool gHall_Flag_EnableStartup = false;	// false->disable hall startup
bool gHall_Flag_CurrentCtrl = false;
bool gHall_Flag_State_Change = false;

uint32_t gHall_timer_now= 0;
uint32_t gHall_timer_prev = 0;
uint32_t gHall_time_delta_now = 0;
uint32_t gHall_time_delta_prev = 0;
uint32_t gHall_time_delta = 0;

uint32_t gHall_speed_scale = USER_SYSTEM_FREQ_MHz*1000000*100/6;
uint32_t gHall_speed_fdb_0p01Hz = 0;
_iq gHall_Speed_0p01hz_to_pu_sf = _IQ((float_t)0.01/(USER_IQ_FULL_SCALE_FREQ_Hz));

uint16_t gHall_PwmCnt = 0;
uint16_t gHall_PwmCntMax = 5000;

uint32_t gHall_Bldc_Cnt = 0;
uint32_t gHall_Fast_Cnt = 0;

void HALLBLDC_Ctrl_Run(void);
void HALLBLDC_State_Check(void);
void HALLBLDC_Ctrl_Stop(void);
void HALLBLDC_Ctrl_PwmSet(uint16_t PwmState, _iq PwmDuty);

// **************************************************************************
// the functions
void main(void)
{
    // IMPORTANT NOTE: If you are not familiar with MotorWare coding guidelines
    // please refer to the following document:
    // C:/ti/motorware/motorware_1_01_00_1x/docs/motorware_coding_standards.pdf

    // Only used if running from FLASH
    // Note that the variable FLASH is defined by the project

    #ifdef FLASH
    // Copy time critical code and Flash setup code to RAM
    // The RamfuncsLoadStart, RamfuncsLoadEnd, and RamfuncsRunStart
    // symbols are created by the linker. Refer to the linker files.
    memCopy((uint16_t *)&RamfuncsLoadStart,(uint16_t *)&RamfuncsLoadEnd,
            (uint16_t *)&RamfuncsRunStart);

    #ifdef CSM_ENABLE
	  //copy .econst to unsecure RAM
	  if(*econst_end - *econst_start)
		{
		  memCopy((uint16_t *)&econst_start,(uint16_t *)&econst_end,(uint16_t *)&econst_ram_load);
		}

	  //copy .switch ot unsecure RAM
	  if(*switch_end - *switch_start)
		{
		  memCopy((uint16_t *)&switch_start,(uint16_t *)&switch_end,(uint16_t *)&switch_ram_load);
		}
    #endif
    #endif

    // initialize the Hardware Abstraction Layer  (HAL)
    // halHandle will be used throughout the code to interface with the HAL
    // (set parameters, get and set functions, etc) halHandle is required since
    // this is how all objects are interfaced, and it allows interface with
    // multiple objects by simply passing a different handle. The use of
    // handles is explained in this document:
    // C:/ti/motorware/motorware_1_01_00_1x/docs/motorware_coding_standards.pdf
    halHandle = HAL_init(&hal,sizeof(hal));

  // check for errors in user parameters
  USER_checkForErrors(&gUserParams);


  // store user parameter error in global variable
  gMotorVars.UserErrorCode = USER_getErrorCode(&gUserParams);


  // do not allow code execution if there is a user parameter error
  if(gMotorVars.UserErrorCode != USER_ErrorCode_NoError)
    {
      for(;;)
        {
          gMotorVars.Flag_enableSys = false;
        }
    }

  // initialize the Clarke modules
  clarkeHandle_I = CLARKE_init(&clarke_I,sizeof(clarke_I));
  clarkeHandle_V = CLARKE_init(&clarke_V,sizeof(clarke_V));

  // initialize the estimator
  estHandle = EST_init((void *)USER_EST_HANDLE_ADDRESS, 0x200);

  // initialize the user parameters
  USER_setParams(&gUserParams);

  // set the hardware abstraction layer parameters
  HAL_setParams(halHandle,&gUserParams);

#ifdef FAST_ROM_V1p6
  {
    CTRL_Handle ctrlHandle = CTRL_init((void *)USER_CTRL_HANDLE_ADDRESS, 0x200);
    CTRL_Obj *obj = (CTRL_Obj *)ctrlHandle;
    obj->estHandle = estHandle;

    // initialize the estimator through the controller
    CTRL_setParams(ctrlHandle,&gUserParams);
    CTRL_setUserMotorParams(ctrlHandle);
    CTRL_setupEstIdleState(ctrlHandle);
  }
#else
  {
    // initialize the estimator
    EST_setEstParams(estHandle,&gUserParams);
    EST_setupEstIdleState(estHandle);
  }
#endif

  // disable Rs recalculation by default
  gMotorVars.Flag_enableRsRecalc = false;
  EST_setFlag_enableRsRecalc(estHandle,false);

  // configure RsOnLine
  EST_setFlag_enableRsOnLine(estHandle,gFlag_enableRsOnLine);
  EST_setFlag_updateRs(estHandle,gFlag_updateRs);
  EST_setRsOnLineAngleDelta_pu(estHandle,_IQmpy(gRsOnLineFreq_Hz, _IQ(1.0/USER_ISR_FREQ_Hz)));
  EST_setRsOnLineId_mag_pu(estHandle,_IQmpy(gRsOnLineId_mag_A, _IQ(1.0/USER_IQ_FULL_SCALE_CURRENT_A)));

  // Calculate coefficients for all filters
  {
    _iq b0 = _IQmpy(gRsOnLinePole_Hz, _IQ(1.0/USER_ISR_FREQ_Hz));
    _iq a1 = b0 - _IQ(1.0);
    EST_setRsOnLineFilterParams(estHandle,EST_RsOnLineFilterType_Current,b0,a1,_IQ(0.0),b0,a1,_IQ(0.0));
    EST_setRsOnLineFilterParams(estHandle,EST_RsOnLineFilterType_Voltage,b0,a1,_IQ(0.0),b0,a1,_IQ(0.0));
  }

  // set the number of current sensors
  setupClarke_I(clarkeHandle_I,USER_NUM_CURRENT_SENSORS);

  // set the number of voltage sensors
  setupClarke_V(clarkeHandle_V,USER_NUM_VOLTAGE_SENSORS);

  // set the pre-determined current and voltage feeback offset values
  gOffsets_I_pu.value[0] = _IQ(I_A_offset);
  gOffsets_I_pu.value[1] = _IQ(I_B_offset);
  gOffsets_I_pu.value[2] = _IQ(I_C_offset);
  gOffsets_V_pu.value[0] = _IQ(V_A_offset);
  gOffsets_V_pu.value[1] = _IQ(V_B_offset);
  gOffsets_V_pu.value[2] = _IQ(V_C_offset);

  // initialize the PID controllers
  {
    _iq maxCurrent_pu = _IQ(USER_MOTOR_MAX_CURRENT / USER_IQ_FULL_SCALE_CURRENT_A);
    _iq maxVoltage_pu = _IQ(USER_MAX_VS_MAG_PU * USER_VD_SF);
    float_t fullScaleCurrent = USER_IQ_FULL_SCALE_CURRENT_A;
    float_t fullScaleVoltage = USER_IQ_FULL_SCALE_VOLTAGE_V;
    float_t IsrPeriod_sec = 1.0 / USER_ISR_FREQ_Hz;
    float_t Ls_d = USER_MOTOR_Ls_d;
    float_t Ls_q = USER_MOTOR_Ls_q;
    float_t Rs = USER_MOTOR_Rs;
    float_t RoverLs_d = Rs/Ls_d;
    float_t RoverLs_q = Rs/Ls_q;
    _iq Kp_Id = _IQ((0.25*Ls_d*fullScaleCurrent)/(IsrPeriod_sec*fullScaleVoltage));
    _iq Ki_Id = _IQ(RoverLs_d*IsrPeriod_sec);
    _iq Kp_Iq = _IQ((0.25*Ls_q*fullScaleCurrent)/(IsrPeriod_sec*fullScaleVoltage));
    _iq Ki_Iq = _IQ(RoverLs_q*IsrPeriod_sec);

    pidHandle[0] = PID_init(&pid[0],sizeof(pid[0]));
    pidHandle[1] = PID_init(&pid[1],sizeof(pid[1]));
    pidHandle[2] = PID_init(&pid[2],sizeof(pid[2]));
    pidHandle[3] = PID_init(&pid[3],sizeof(pid[3]));

    PID_setGains(pidHandle[0],_IQ(0.2),_IQ(0.005),_IQ(0.0));
   // PID_setMinMax(pidHandle[0],-maxCurrent_pu,maxCurrent_pu);
    PID_setMinMax(pidHandle[0],_IQ(0.0),maxCurrent_pu);
    PID_setUi(pidHandle[0],_IQ(0.0));
    pidCntSpeed = 0;

    PID_setGains(pidHandle[1],Kp_Id,Ki_Id,_IQ(0.0));
    PID_setMinMax(pidHandle[1],-maxVoltage_pu,maxVoltage_pu);
    PID_setUi(pidHandle[1],_IQ(0.0));

    PID_setGains(pidHandle[2],Kp_Iq,Ki_Iq,_IQ(0.0));
    PID_setMinMax(pidHandle[2],_IQ(0.0),_IQ(0.0));
    PID_setUi(pidHandle[2],_IQ(0.0));

    PID_setGains(pidHandle[3],Kp_Iq,Ki_Iq,_IQ(0.0));
    PID_setMinMax(pidHandle[3],_IQ(0.0),_IQ(0.0));
    PID_setUi(pidHandle[3],_IQ(0.0));
  }

  // initialize the speed reference in kilo RPM where base speed is USER_IQ_FULL_SCALE_FREQ_Hz
  gMotorVars.SpeedRef_krpm = _IQmpy(_IQ(30.0), gSpeed_hz_to_krpm_sf);

  // initialize the inverse Park module
  iparkHandle = IPARK_init(&ipark,sizeof(ipark));

  // initialize and configure offsets using filters
  {
    uint16_t cnt = 0;
    _iq b0 = _IQ(gUserParams.offsetPole_rps/(float_t)gUserParams.ctrlFreq_Hz);
    _iq a1 = (b0 - _IQ(1.0));
    _iq b1 = _IQ(0.0);

    for(cnt=0;cnt<6;cnt++)
      {
        filterHandle[cnt] = FILTER_FO_init(&filter[cnt],sizeof(filter[0]));
        FILTER_FO_setDenCoeffs(filterHandle[cnt],a1);
        FILTER_FO_setNumCoeffs(filterHandle[cnt],b0,b1);
        FILTER_FO_setInitialConditions(filterHandle[cnt],_IQ(0.0),_IQ(0.0));
      }

    gMotorVars.Flag_enableOffsetcalc = false;
  }

  // initialize the space vector generator module
  svgenHandle = SVGEN_init(&svgen,sizeof(svgen));

  // Initialize and setup the 100% SVM generator
  svgencurrentHandle = SVGENCURRENT_init(&svgencurrent,sizeof(svgencurrent));

  // setup svgen current
  {
    float_t minWidth_microseconds = 2.0;
    uint16_t minWidth_counts = (uint16_t)(minWidth_microseconds * USER_SYSTEM_FREQ_MHz);
    float_t fdutyLimit = 0.5-(2.0*minWidth_microseconds*USER_PWM_FREQ_kHz*0.001);
    _iq dutyLimit = _IQ(fdutyLimit);

    SVGENCURRENT_setMinWidth(svgencurrentHandle, minWidth_counts);
    SVGENCURRENT_setIgnoreShunt(svgencurrentHandle, use_all);
    SVGENCURRENT_setMode(svgencurrentHandle,all_phase_measurable);
    SVGENCURRENT_setVlimit(svgencurrentHandle,dutyLimit);
  }

  // initialize the speed reference trajectory
  trajHandle_spd = TRAJ_init(&traj_spd,sizeof(traj_spd));

  // configure the speed reference trajectory
  TRAJ_setTargetValue(trajHandle_spd,_IQ(0.0));
  TRAJ_setIntValue(trajHandle_spd,_IQ(0.0));
  TRAJ_setMinValue(trajHandle_spd,_IQ(-1.0));
  TRAJ_setMaxValue(trajHandle_spd,_IQ(1.0));
  TRAJ_setMaxDelta(trajHandle_spd,_IQ(USER_MAX_ACCEL_Hzps / USER_IQ_FULL_SCALE_FREQ_Hz / USER_ISR_FREQ_Hz));

  // initialize the Id reference trajectory
  trajHandle_Id = TRAJ_init(&traj_Id,sizeof(traj_Id));

  if(USER_MOTOR_TYPE == MOTOR_Type_Pm)
    {
      // configure the Id reference trajectory
      TRAJ_setTargetValue(trajHandle_Id,_IQ(0.0));
      TRAJ_setIntValue(trajHandle_Id,_IQ(0.0));
      TRAJ_setMinValue(trajHandle_Id,_IQ(-USER_MOTOR_MAX_CURRENT / USER_IQ_FULL_SCALE_CURRENT_A));
      TRAJ_setMaxValue(trajHandle_Id,_IQ(USER_MOTOR_MAX_CURRENT / USER_IQ_FULL_SCALE_CURRENT_A));
      TRAJ_setMaxDelta(trajHandle_Id,_IQ(USER_MOTOR_RES_EST_CURRENT / USER_IQ_FULL_SCALE_CURRENT_A / USER_ISR_FREQ_Hz));

      // Initialize field weakening
      fwHandle = FW_init(&fw,sizeof(fw));
      FW_setFlag_enableFw(fwHandle, false); // Disable field weakening
      FW_clearCounter(fwHandle); // Clear field weakening counter
      FW_setNumIsrTicksPerFwTick(fwHandle, FW_NUM_ISR_TICKS_PER_CTRL_TICK); // Set the number of ISR per field weakening ticks
      FW_setDeltas(fwHandle, FW_INC_DELTA, FW_DEC_DELTA); // Set the deltas of field weakening
      FW_setOutput(fwHandle, _IQ(0.0)); // Set initial output of field weakening to zero
      FW_setMinMax(fwHandle,_IQ(USER_MAX_NEGATIVE_ID_REF_CURRENT_A/USER_IQ_FULL_SCALE_CURRENT_A),_IQ(0.0)); // Set the field weakening controller limits
    }
  else
    {
      // configure the Id reference trajectory
      TRAJ_setTargetValue(trajHandle_Id,_IQ(0.0));
      TRAJ_setIntValue(trajHandle_Id,_IQ(0.0));
      TRAJ_setMinValue(trajHandle_Id,_IQ(0.0));
      TRAJ_setMaxValue(trajHandle_Id,_IQ(USER_MOTOR_MAGNETIZING_CURRENT / USER_IQ_FULL_SCALE_CURRENT_A));
      TRAJ_setMaxDelta(trajHandle_Id,_IQ(USER_MOTOR_MAGNETIZING_CURRENT / USER_IQ_FULL_SCALE_CURRENT_A / USER_ISR_FREQ_Hz));
    }
    // initialize the CPU usage module
    cpu_timeHandle = CPU_TIME_init(&cpu_time,sizeof(cpu_time));
    CPU_TIME_setParams(cpu_timeHandle, PWM_getPeriod(halHandle->pwmHandle[0]));
  // setup faults
  HAL_setupFaults(halHandle);

  // initialize the interrupt vector table
  HAL_initIntVectorTable(halHandle);

  // enable the ADC interrupts
  HAL_enableAdcInts(halHandle);

  // enable global interrupts
  HAL_enableGlobalInts(halHandle);

  // enable debug interrupts
  HAL_enableDebugInt(halHandle);

  // disable the PWM
  HAL_disablePwm(halHandle);

  // compute scaling factors for flux and torque calculations
  gFlux_pu_to_Wb_sf = USER_computeFlux_pu_to_Wb_sf();
  gFlux_pu_to_VpHz_sf = USER_computeFlux_pu_to_VpHz_sf();
  gTorque_Ls_Id_Iq_pu_to_Nm_sf = USER_computeTorque_Ls_Id_Iq_pu_to_Nm_sf();
  gTorque_Flux_Iq_pu_to_Nm_sf = USER_computeTorque_Flux_Iq_pu_to_Nm_sf();

  // enable the system by default
  gMotorVars.Flag_enableSys = true;

#ifdef DRV8301_SPI
  // turn on the DRV8301 if present
  HAL_enableDrv(halHandle);
  // initialize the DRV8301 interface
  HAL_setupDrvSpi(halHandle,&gDrvSpi8301Vars);
#endif
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

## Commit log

2017-05-19 adding some calculations and untouched source files from motorware, just the files I'm likely to modify, HAL, project files etc.
    [motorware_selecting_user_variables.xlsx]
2017-05-19 added schematic, PCB design for Zytek replacement control board. Modified motorware HAL files to work with this design
    [BOM.xlsx, PSU.SchDoc, connector.SchDoc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]
2017-06-10 tweaked isolated voltage sensors
    [motorware_selecting_user_variables.xlsx, voltage_conditioning.SchDoc, zytek_ctl.SchDoc]
2017-06-14 issues with bringup, changed current sensor polarity and various parameters. Still hitting overcurrent
    [hal.c, hal.h, proj_lab01b.c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]
2017-06-14 last change for positive current feedback
2017-06-15 sorted control issues, identified motor at 100V
    [hal.c, proj_lab01b.c, proj_lab02d.c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]
2017-08-18 attempt at lab11b with hall sensor startup
2017-11-12 resized rooms
    [zytek_ctl.PrjPcb]
